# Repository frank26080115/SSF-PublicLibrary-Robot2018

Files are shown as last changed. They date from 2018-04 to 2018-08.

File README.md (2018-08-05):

# SSF-PublicLibrary-Robot2018

This repo contains the hardware, software, and courseware of a small robotics STEM education program. This program is targeting ages 12+, involves 3 live classes held at South San Francisco Public Library, and a robot that's insanely cheap but also incredibly educational.

Perhaps the data here is useful for other educational organizations on a budget.

Please click "Clone or Download" and then "Download ZIP". When the ZIP file is downloaded, unzip it somewhere and open "courseware/index.htm" with a web browser. This will start the course. All the courseware is written as web pages, with pictures, videos, and interactive demos.

The lessons are also hosted on my own website, http://eleccelerator.com/ssfpl_robotics_class_2018/

## Software Required

- Arduino 1.8.1 (this is what SSF Public Library has currently installed)
- Onshape account (free web browser based CAD software that mimics SolidWorks)

## Thanks to: [Microchip Technology](https://www.microchip.com/)

A big thanks to [Microchip Technology](https://www.microchip.com/). These guys manufacture the chip in the middle of your Arduino. My professional contacts at their local office generously donated an insane amount of screwdrivers and backpacks. These classes would not have been possible without their help. Their kindness will not be forgotten.

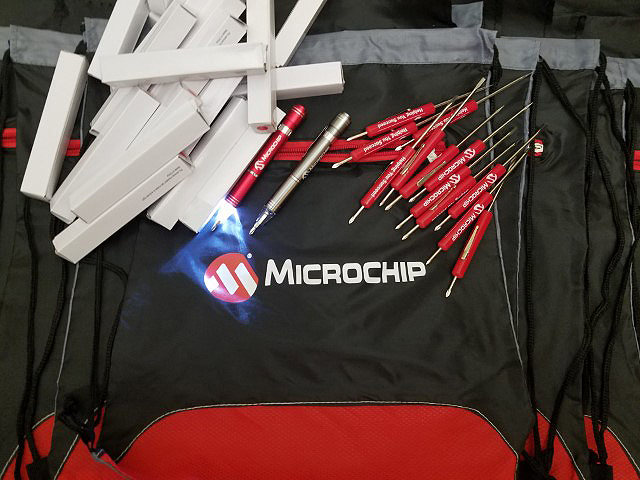
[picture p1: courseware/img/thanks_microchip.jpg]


Personally I thank Microchip for jumpstarting my own path in this hobby and career. Microchip Technology is a huge supporter of STEM programs, I definitely have many of their dev kits simply because they handed them out to me in university. Even when I was a poor highschooler, I got started with their PIC microcontrollers because they were essentially free. I truly believe they are the reason why I am insanely good at writing low-level bare-metal embedded firmware. By the time Arduino Diecimila (the first Arduino with USB) was available, I immediately outgrew the Arduino IDE because of just how far using a PIC has pushed me.

## Thanks to: [Adafruit Industries](https://www.adafruit.com/)

[Adafruit Industries](https://www.adafruit.com/) is a founding pillar of the maker movement from the very beginning, and a [champion for women engineers and entrepreneurs](https://www.adafruit.com/about). Limor "Ladyada" Fried and Phillip Torrone (former senior editor at Make: Magazine, Hackaday, Popular Science, Howtoons) donated all the soldering irons we need that makes these classes possible. These irons are the good stuff, coated tips, adjustable ceramic heaters, fire-proof wiring!

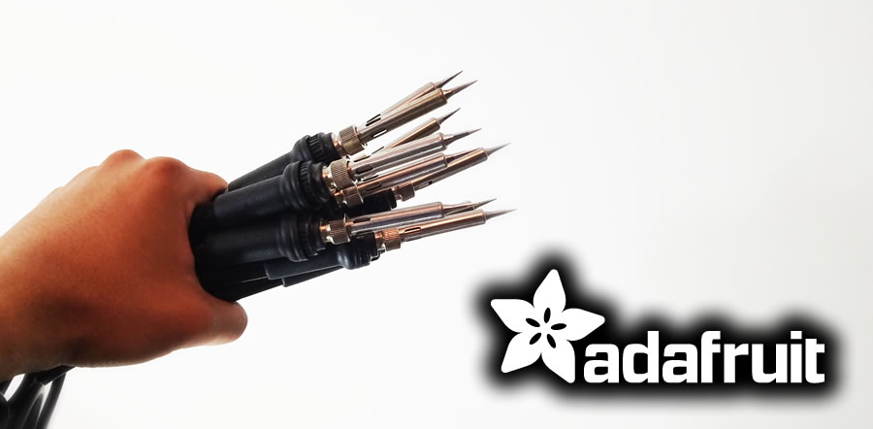
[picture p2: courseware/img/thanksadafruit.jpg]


As a huge supporter of STEAM education, Adafruit Industries have written literally [thousands of guides and tutorials](https://learn.adafruit.com/), along side their amazing collection of products that makes it easy for everyday people to accomplish what used to be impossible. How do I know they are so good? I used to work for Adafruit myself, I wrote some of those tutorials and designed some of those products. Even today my real job's engineering department use their stuff regularly, their breakout boards are just so convenient for quick prototypes. Everything is manufactured proudly on home turf in their New York City office. I recommend all hobbyists to follow [their blog](https://blog.adafruit.com/), it's a good mix of electronics, 3D printing, art, and other fun news.

## Thanks to: [PCBWay](https://www.pcbway.com/)

[PCBWay](https://www.pcbway.com/) is a speedy and cheap PCB manufacturer and electronics assembly company. They generously provided us with multi-colour PCBs for free, so your robots can be pretty and more unique.

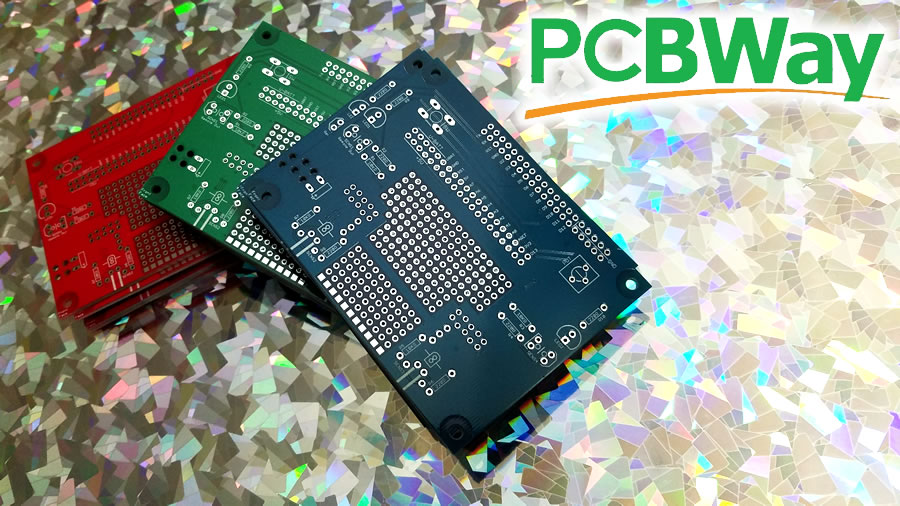
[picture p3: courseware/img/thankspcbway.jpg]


Their service is speedy and at a price that was unheard of before the maker movement took off, making it more accessible to hobbyists and students, allowing the little guys to keep up with the big tech companies. PCBWay also do a lot of [community outreach](https://www.pcbway.com/project/sponsor/) to hobbyists and student teams, hosting contests and offering sponsorships.

Their PCBs are pretty high quality, there's nothing to complain about. Great looking silkscreen. Soldermask and drills are on point. Edges are milled clean. No splatter with the plating. No hassle using their website to order. Each one of our robot PCBs would cost roughly $3.50 each including shipping, and take one week from time-of-order to your doorstep. Great job PCBWay.

## Thanks to: [Silicon Labs](https://www.silabs.com/)

I reached out to people I know at the local [Silicon Labs](https://www.silabs.com/) office, and they gave us a big box of goodies to encourage people to participate in STEM programs at our library.

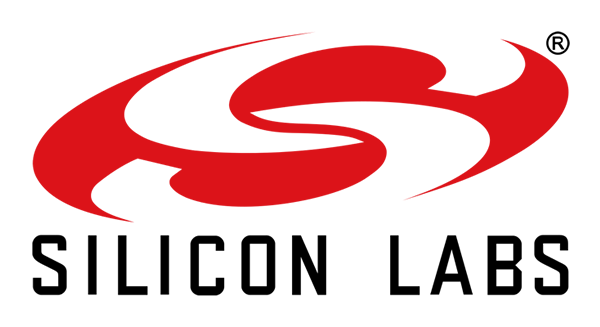
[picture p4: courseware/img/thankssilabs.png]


They are a company who manufacture a lot of different microchips, such as the USB interface chips that hobbyists often use to debug the Raspberry Pi and other embedded Linux platforms. If you are into the drone racing hobby, most likely your drone already has four microcontrollers made by Silicon Labs. They've been growing rapidly in the past decade and is currently well known for having unique, high performance, and low power products, as well as legacy products that are solid and dirt cheap.

## Thanks to: [Hackaday](https://hackaday.com/)

Hackaday always have a special place in my life, providing me with constant motivation and keeping me up-to-date on both my hobby and professional life. They are literally the biggest reason why I am working a dream job in sunny California. I think their blog is inspirational to everybody here and so they gave me a pile of stickers to give to my class!

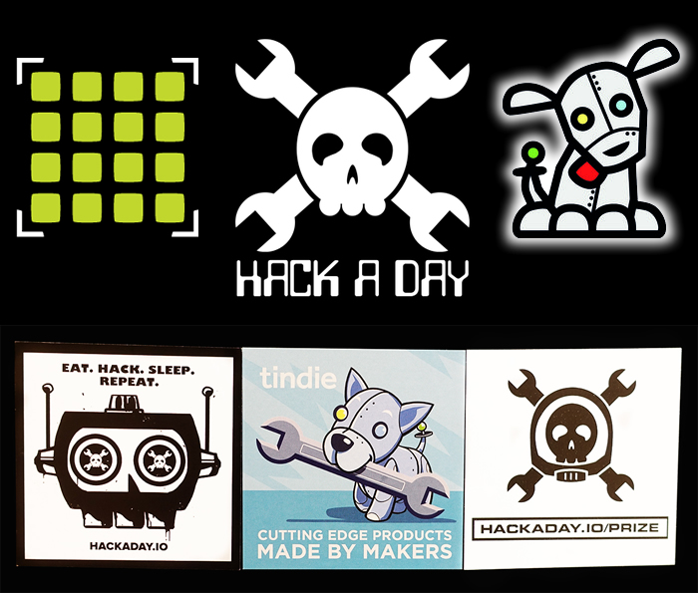
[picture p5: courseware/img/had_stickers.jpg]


They are the host of an excellent online community at [Hackaday.io](https://hackaday.io/), hosts awesome events such as the [Hackaday SuperConference](https://hackaday.com/tag/hackaday-superconference/) and their [Hackaday Prize](https://hackaday.io/prize), and also they run the beloved [Tindie](https://www.tindie.com/) where creative makers and hackers can sell their creations.

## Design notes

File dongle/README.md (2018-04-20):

## What is "dongle"?

The problem is that the library's laptops are locked-down. I can't install device drivers or applications on them, and I can't depend on the library's IT staff to do so either. The Arduino Nanos that cost only $4 each have a CH430 chip as the USB-to-UART converter and that definitely needs a driver to be installed in order to work.

Some form of USB-to-UART is needed in order to communicate with the Arduino Nano bootloader. Ideally, with auto-reset capability.

Well... the library's laptops already have Arduino 1.8.1 installed. Which means that the default virtual COM drivers for Arduino's ATmega8U2 must already be installed as well.

The "dongle" directory contains code for a PSoC that turns it into a USB-to-UART converter. It will use the same VID and PID as the Arduino's ATmega8U2.

The hardware will be the detachable KitProg from Cypress PSoC dev kits. I have plenty of these to give away because we typically break them off from the dev kits at work.

There is no capacitor for the DTS signal that is meant for auto-reset, instead, a simple pulse with a delay simulates the capacitor.

So in the end, for zero cost to me personally, I provide about a dozen USB-to-serial converters to the library that works without additional driver installation. :-)

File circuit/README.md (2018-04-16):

This directory contains the circuit schematic, PCB layout, and PCB gerber files for the robot's circuit board.

The file formats are for CadSoft EAGLE 6.4.0

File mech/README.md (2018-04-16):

This directory includes the STEP, IGES, STL, and GCODE files for the 3D printed body of the robot, and its other parts as well

The actual parametric CAD model of the robot is hosted as public documents on Onshape

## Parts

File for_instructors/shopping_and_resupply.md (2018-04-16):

# Shopping and Resupply

## Tools

### Soldering

There needs to be several soldering irons and accessories for soldering

- soldering iron
- soldering iron stand
- brass wool or damp sponge for cleaning the iron tips
- desoldering braid for fixing mistakes
- desoldering pump for fixing mistakes (not as good as braid but still required)
- solder, rosin core, preferably 60/40 or 63/37 mix
- flush cutters (wire cutters)
- optional: wire strippers capable stripping 26 AWG wire

### Hand Tools

- needle nose plier
- PH0 screwdriver
- hot glue gun

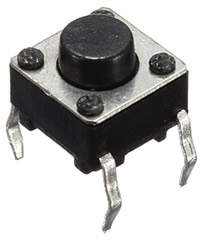
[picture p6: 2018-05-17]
courseware/img/parts/buttonswitch.jpg

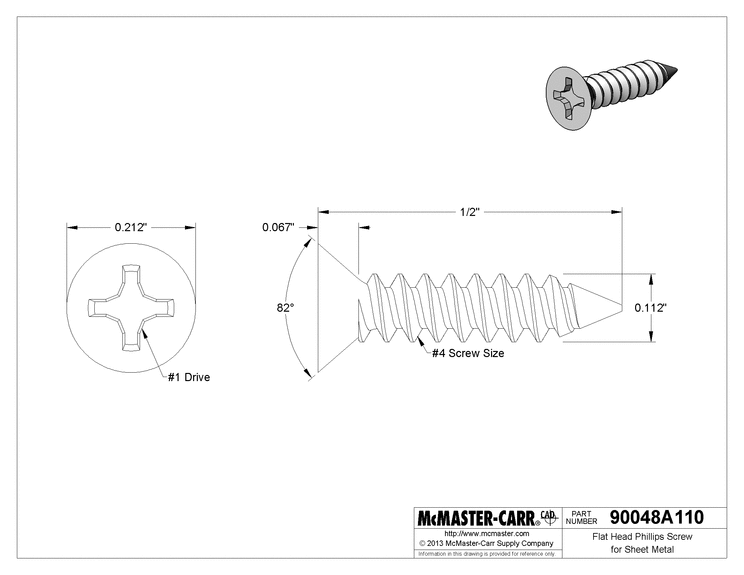
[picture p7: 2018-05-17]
courseware/img/parts/battholderscrew.gif

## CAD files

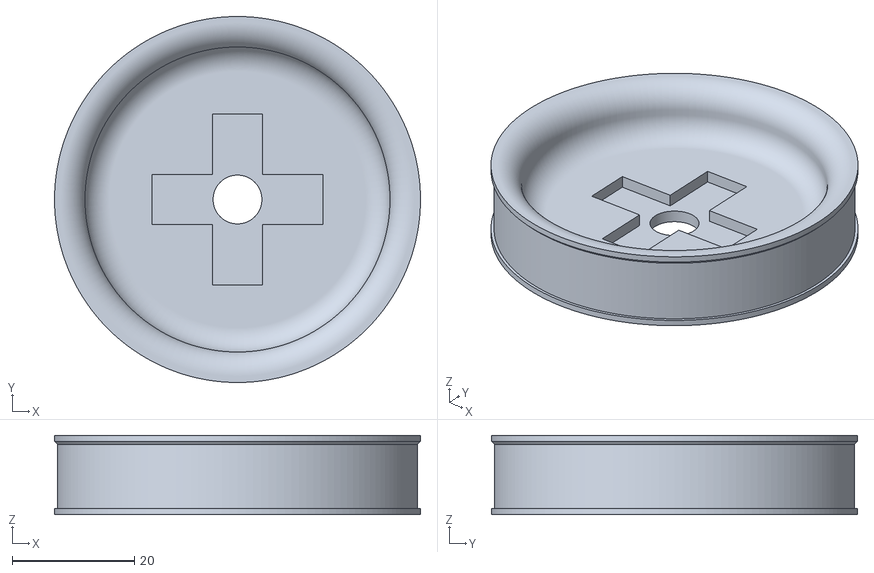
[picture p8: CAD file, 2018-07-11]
mech/wheel_loose.stl
60.0 x 60.0 x 13.0

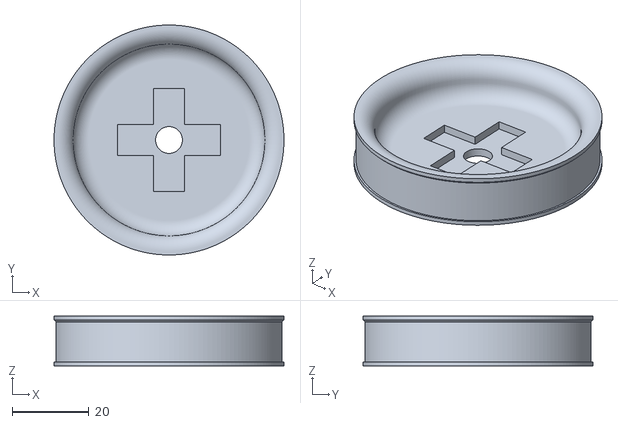
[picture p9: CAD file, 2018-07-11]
mech/wheel.stl
60.0 x 60.0 x 13.0

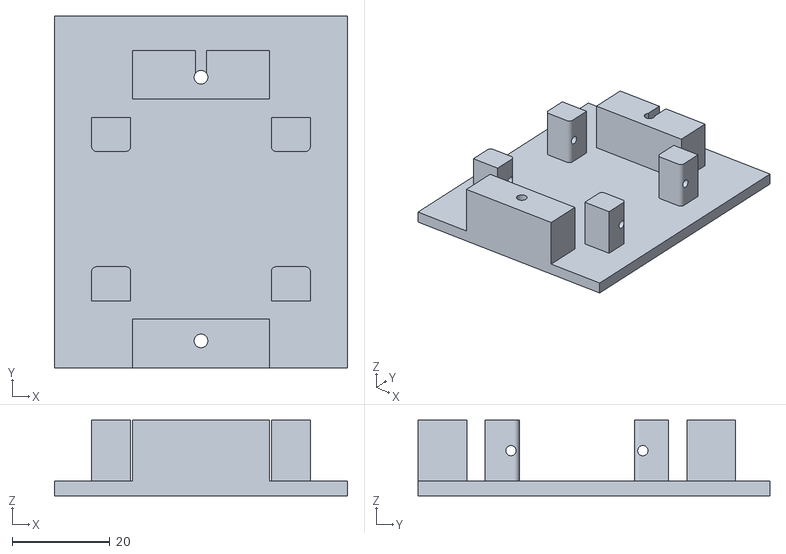
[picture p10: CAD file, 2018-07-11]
mech/robotbody_easierprint.stl
60.0 x 72.0 x 15.5

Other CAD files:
mech/robotbody.stl

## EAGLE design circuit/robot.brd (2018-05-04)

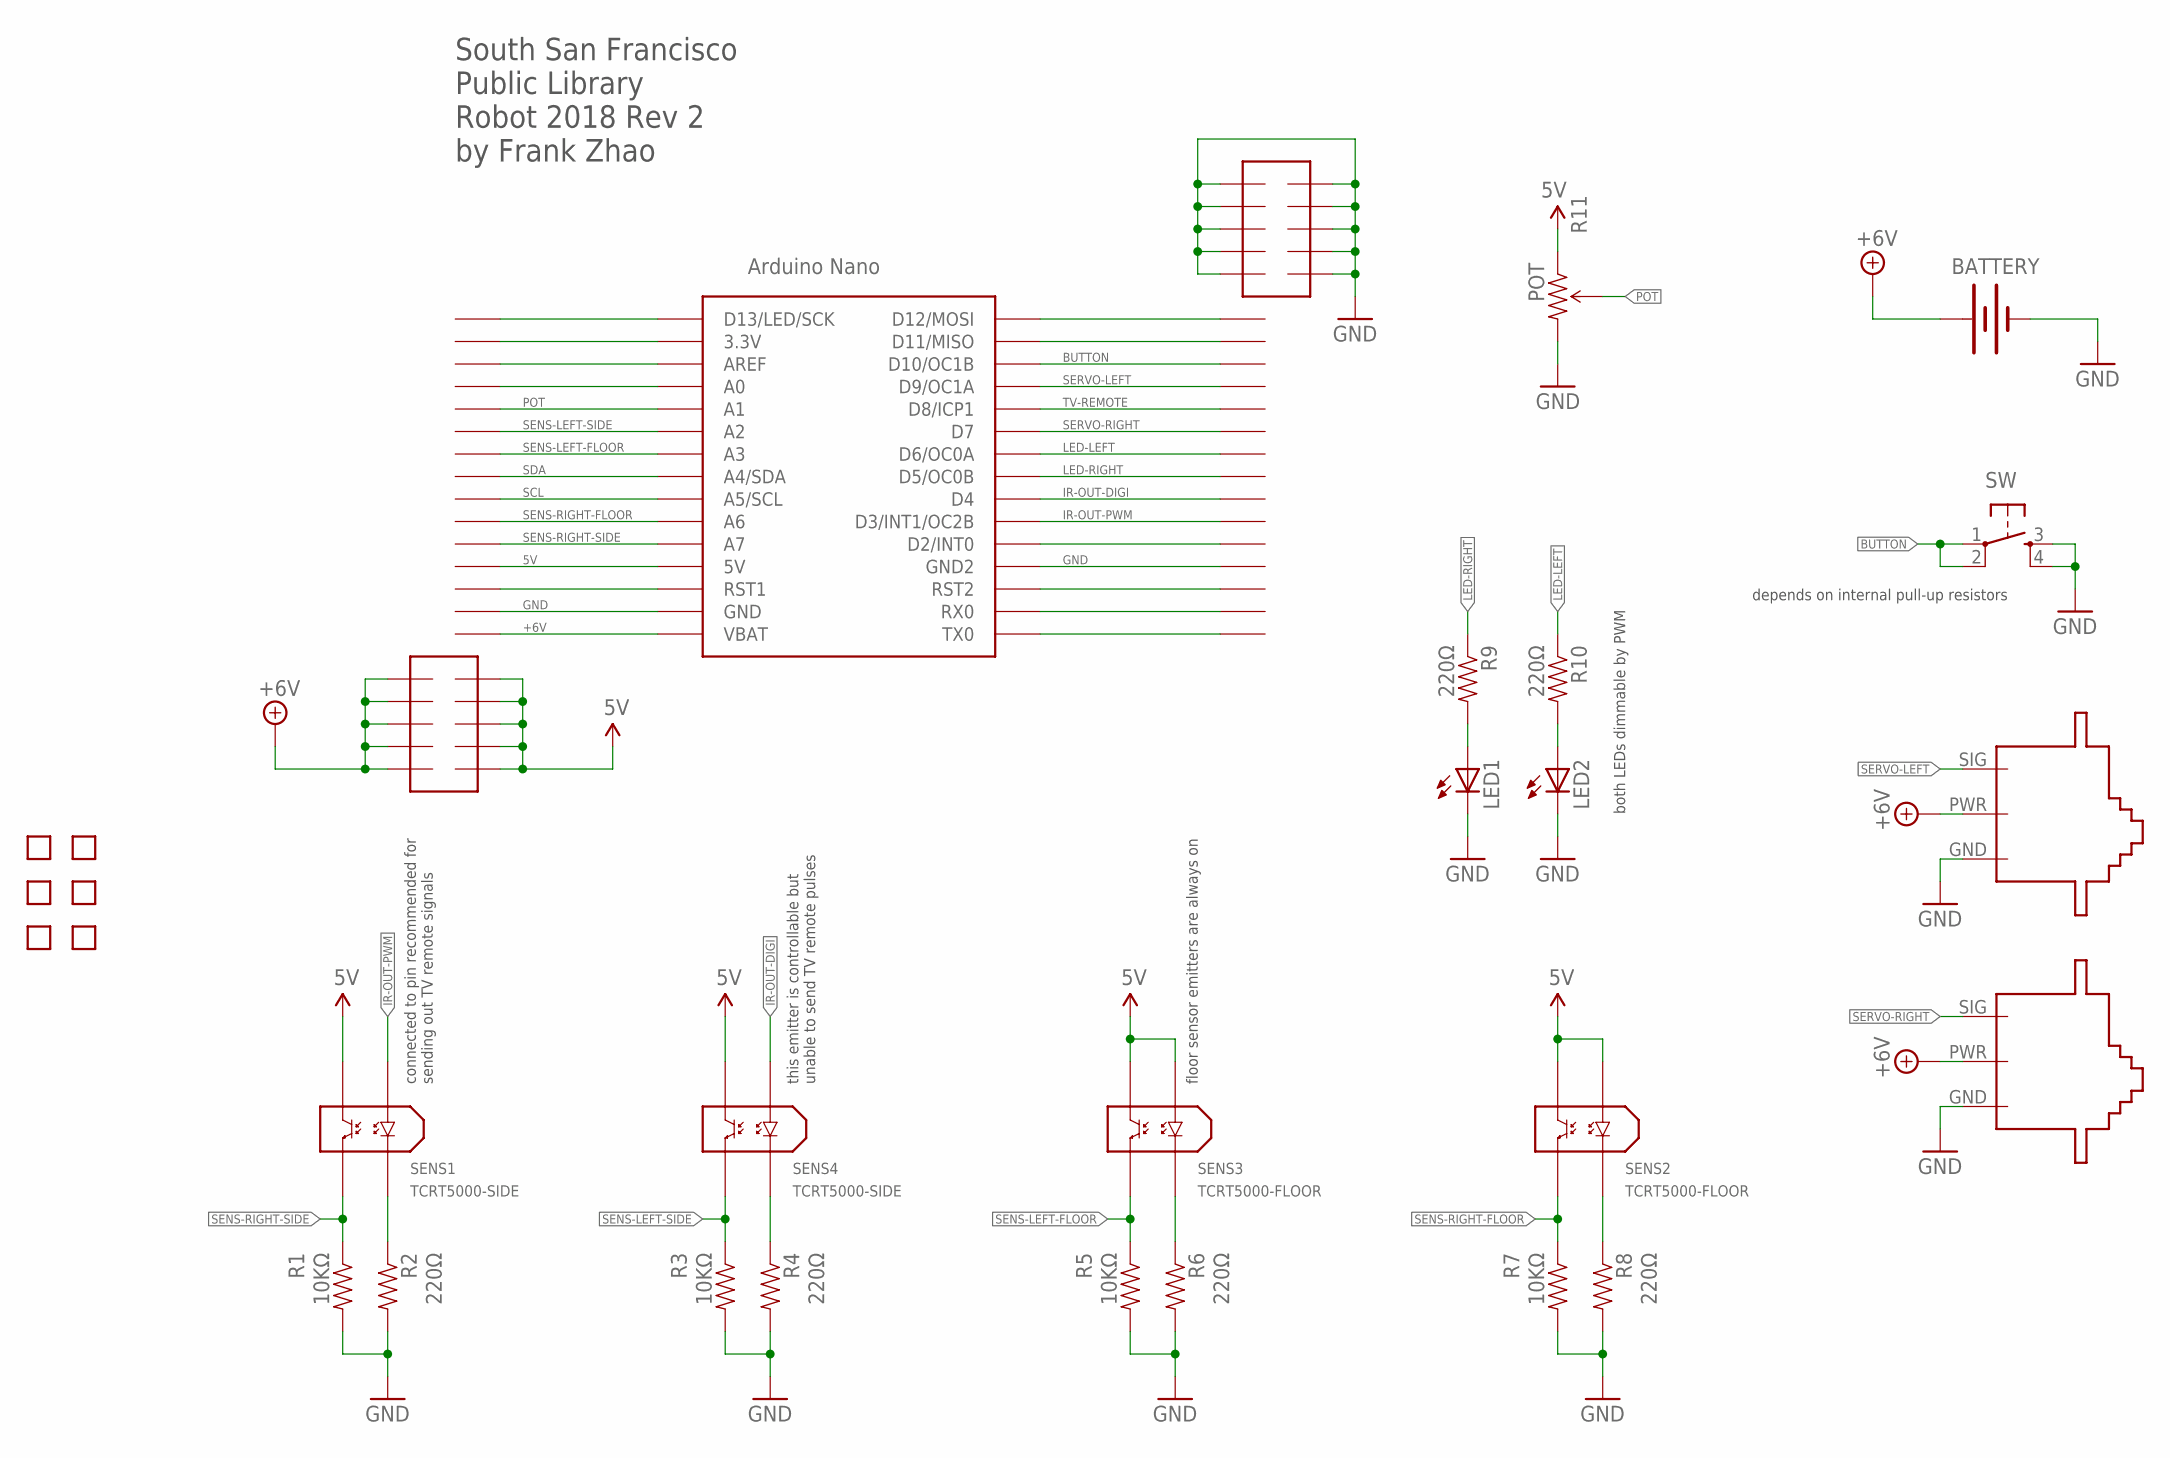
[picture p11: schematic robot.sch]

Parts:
BATTERY: BATTERY-WIRE-CONN; BATT-WIRE-CONN
LED1, LED2: LED5MM
M1: SERVO-FLIPPED
M2: SERVO-1; SERVO
R1, R3, R5, R7: 10KΩ; AXIAL-0.3
R2, R4, R6, R8, R9, R10: 220Ω; AXIAL-0.3
R11: POT; TRIM_POT_PTH
SENS1, SENS4: TCRT5000-SIDE
SENS2, SENS3: TCRT5000-FLOOR
SW: TAC_SWITCHPTH; TACTILE-PTH
U5: NANO
U$1: ROBOT-BODY-HOLDER
U$8: PROTO-AREA-MID; PROTO-AREA-1
U$9: TEXT-INFO
U$10, U$11, U$12, U$13: HOLE; HOLE-2MM
X1, X2: NANO-HEADER-SURROUND

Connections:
5V: R11.1 (CCW), SENS1.COL, SENS2.AN, SENS2.COL, SENS3.AN, SENS3.COL, SENS4.COL, U5.5V, X2.4, X2.E6, X2.E7, X2.E8, X2.E9, X2.E10
+6V: BATTERY.POS (+), M1.PWR, M2.PWR, U5.RAW (VBAT), X2.1, X2.E1, X2.E2, X2.E3, X2.E4, X2.E5
A0: U5.A0, X2.12
BUTTON: SW.1, SW.2, U5.D10 (D10/OC1B), X1.3
GND: BATTERY.NEG (-), LED1.K (C), LED2.K (C), M1.GND, M2.GND, R1.P$2 (2), R2.P$2 (2), R3.P$2 (2), R4.P$2 (2), R5.P$2 (2), R6.P$2 (2), R7.P$2 (2), R8.P$2 (2), R11.3 (CW), SW.3, SW.4, U5.GND, U5.GND1 (GND2), X1.12, X1.E1, X1.E2, X1.E3, X1.E4, X1.E5, X1.E6, X1.E7, X1.E8, X1.E9, X1.E10, X2.2
IR-OUT-DIGI: SENS4.AN, U5.D4, X1.9
IR-OUT-PWM: SENS1.AN, U5.D3 (D3/INT1/OC2B), X1.10
LED-LEFT: R10.P$1 (1), U5.D6 (D6/OC0A), X1.7
LED-RIGHT: R9.P$1 (1), U5.D5 (D5/OC0B), X1.8
unnamed: R2.P$1 (1), SENS1.CAT
unnamed: R4.P$1 (1), SENS4.CAT
unnamed: R6.P$1 (1), SENS3.CAT
unnamed: R8.P$1 (1), SENS2.CAT
unnamed: LED1.A, R9.P$2 (2)
unnamed: LED2.A, R10.P$2 (2)
unnamed: U5.3.3V, X2.14
unnamed: U5.AREF, X2.13
unnamed: U5.RST (RST1), X2.3
unnamed: U5.D13 (D13/LED/SCK), X2.15
unnamed: U5.D12 (D12/MOSI), X1.1
unnamed: U5.D11 (D11/MISO), X1.2
unnamed: U5.D2 (D2/INT0), X1.11
unnamed: U5.RST1 (RST2), X1.13
unnamed: U5.RX0, X1.14
unnamed: U5.TX0, X1.15
POT: R11.2 (WIPER), U5.A1, X2.11
SCL: U5.A5 (A5/SCL), X2.7
SDA: U5.A4 (A4/SDA), X2.8
SENS-LEFT-FLOOR: R5.P$1 (1), SENS3.EM, U5.A3, X2.9
SENS-LEFT-SIDE: R3.P$1 (1), SENS4.EM, U5.A2, X2.10
SENS-RIGHT-FLOOR: R7.P$1 (1), SENS2.EM, U5.A6, X2.6
SENS-RIGHT-SIDE: R1.P$1 (1), SENS1.EM, U5.A7, X2.5
SERVO-LEFT: M2.SIG, U5.D9 (D9/OC1A), X1.4
SERVO-RIGHT: M1.SIG, U5.D7, X1.6
TV-REMOTE: U5.D8 (D8/ICP1), X1.5

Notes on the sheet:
connected to pin recommended for sending out TV remote signals
this emitter is controllable but unable to send TV remote pulses
floor sensor emitters are always on
depends on internal pull-up resistors
both LEDs dimmable by PWM

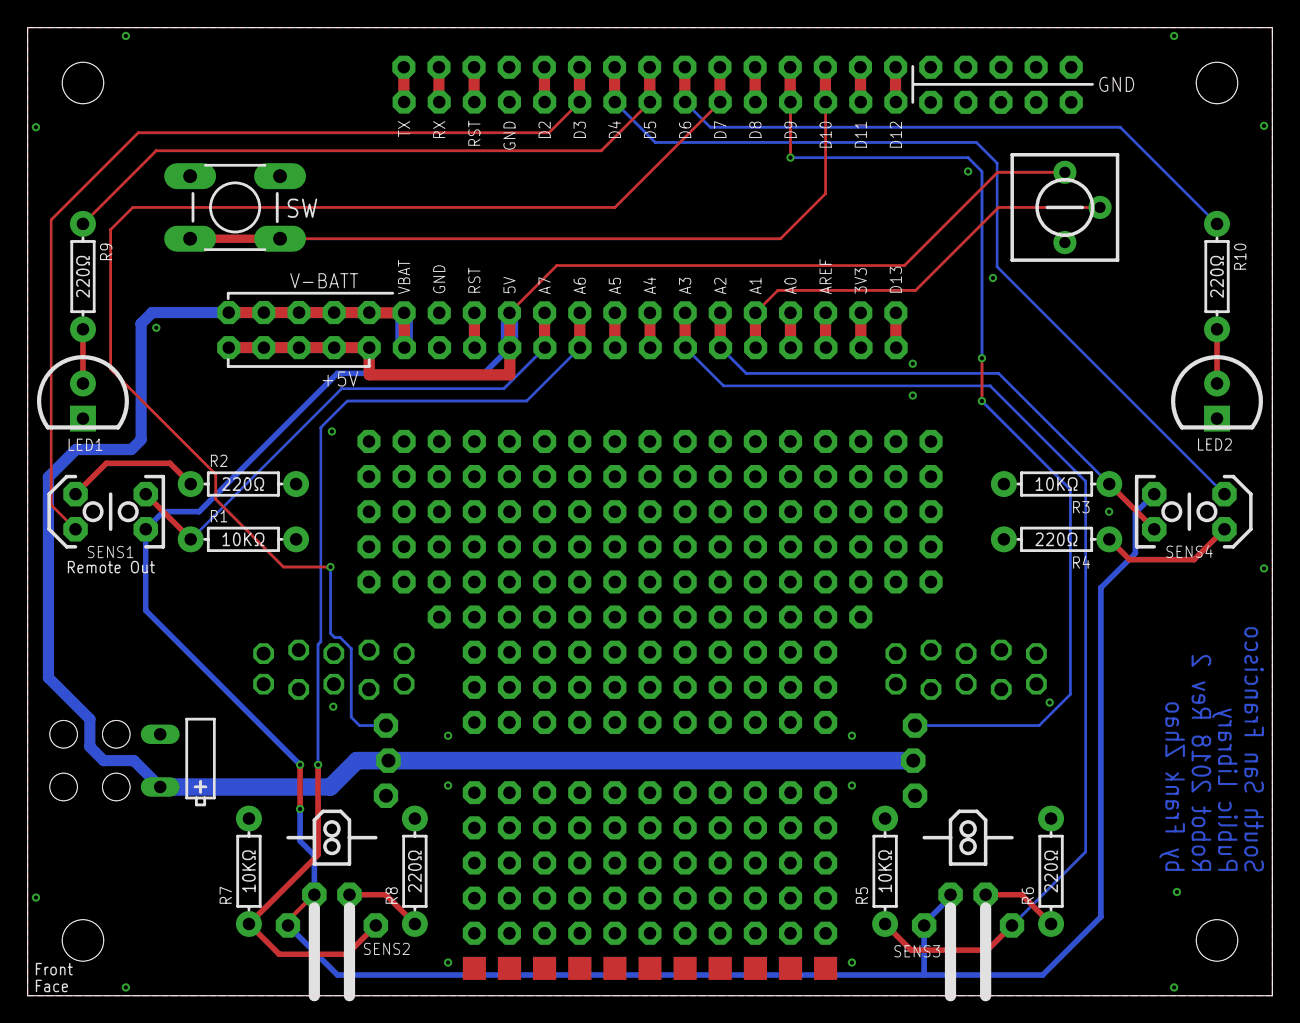
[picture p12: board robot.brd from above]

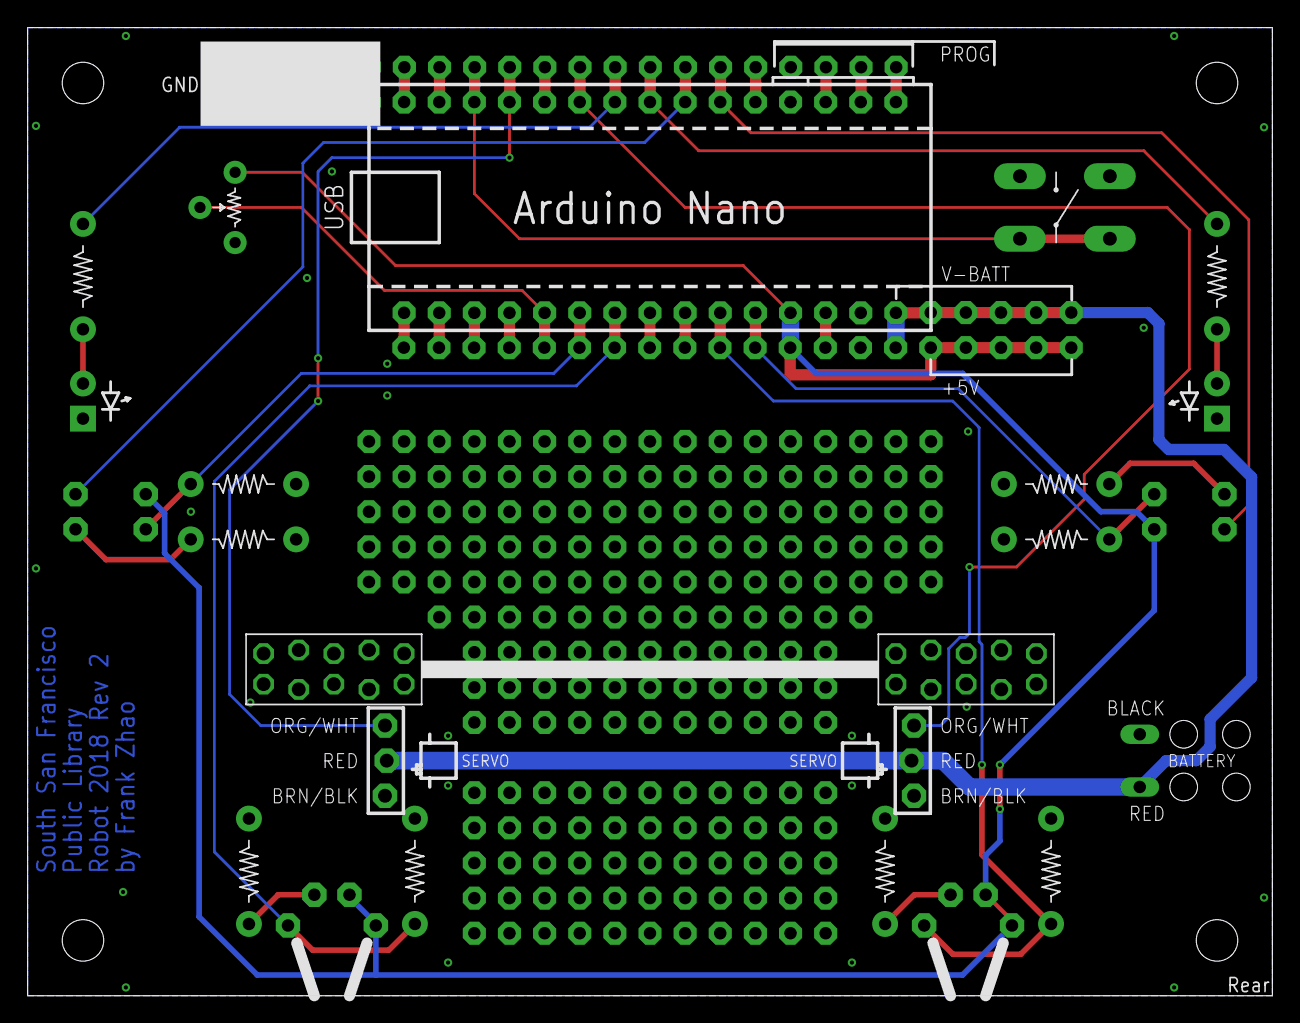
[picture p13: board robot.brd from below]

Board: 2 copper layers, 90.0 x 70.0 mm, 31 parts (7 on the bottom side), 35 nets.

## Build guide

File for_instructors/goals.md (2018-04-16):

# Goals

### Works at SSF Public Library

Everything is designed taking into account what the library can and cannot do. The class size limit accounts for the room size and staff availability. The complexity of a class is designed around 1 hour sessions. The software used is either web browser based or already installed on the library computers. 

### Extended Learning

The robot can be expanded upon. Components can be added to the circuit board, and a breadboard can be stuck to the back of the robot. Extra lessons can be given to students who wants to do upgrades.

Participants will compete in line-following races and mini sumo wrestling. They are encouraged to come back with improvements and a leader board will be kept for the small community. 

### Economical

All the components of the robot are dirt cheap, available in bulk from AliExpress, Amazon, or eBay. Leftover components can be used later for a repeat of the program or for other programs. Many of the components are already in the SSF Public Library's inventory.

We want hobby robotics to appear cheap and accessible to everyone. Which also encourages continued learning.

The time per class is carefully minimized while maximizing concepts being taught. The rooms at the library are shared between many different programs, the only class that requires a room is the soldering session. The rest can take place in a quiet corner of the library.

### Instant Gratification

Success encourages more success. At every step, the student should feel like they have accomplished something. The live soldering class will attempt to get the robot moving as soon as possible.

This library does have two 3D printers that can be used to print what the students create.

### Ease of Instruction

Videos are prepared well ahead of the class, while live demonstration is still used. The videos are short loops that can be left on a projector. This will allow the instructor (me) to help a pupil while other pupils can still watch the videos, or even skip ahead while the instructor helps somebody who is slightly behind.

The videos are silent with text captions. Good for accessibility, and a library.

The circuit board is well labeled with graphics that minimizes chances of mistakes.

NO MATH ALLOWED IN MY COURSEWARE :-) we don't want to bore anybody

### Starting from Minimal Components

The robot kits on Amazon all feel like good deals, but they don't teach anything. Those are all designed to look like you are getting "value" with a lot of parts, and made hard to fail at so they get good 5 star reviews. In doing so, they hide a lot of concepts that enable creativity.

For example, most of those kits on Amazon feature a TCRT5000 sensor but they are pre-assembled into a comparator circuit that outputs 1 or 0. Whereas the class here will link the concept of a potentiometer voltage divider to the phototransistor replacing one of two resistors in a voltage divider, thus forming an amplifier that reacts to light.

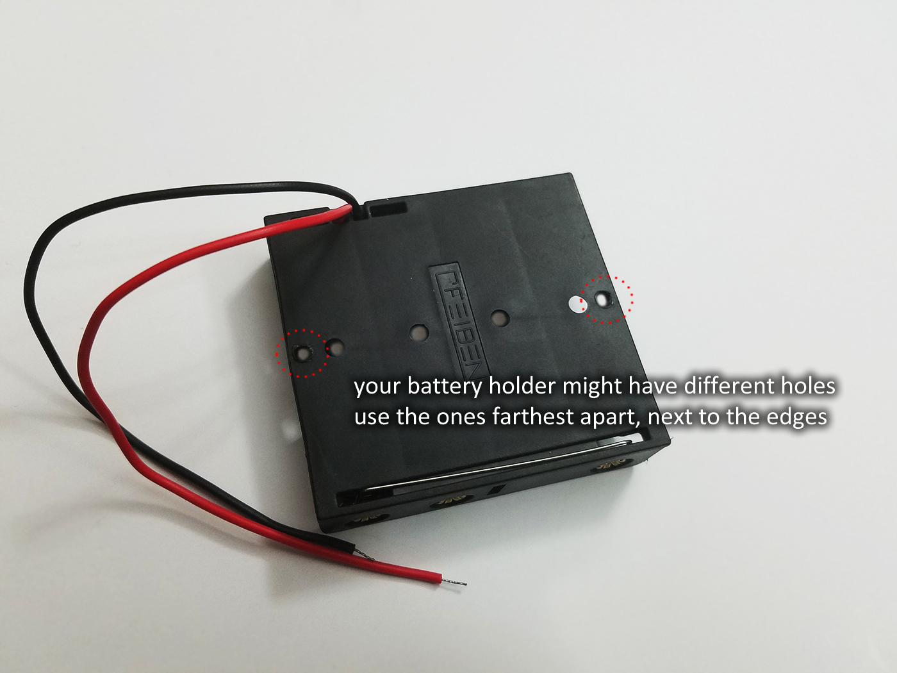
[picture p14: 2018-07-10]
courseware/img/instruct/battholder_diffholes.jpg

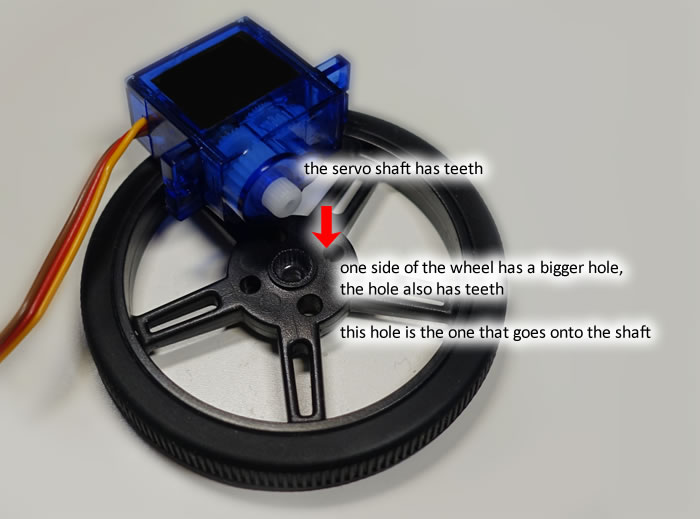
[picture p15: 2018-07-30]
courseware/img/instruct/servoshaftteeth.jpg

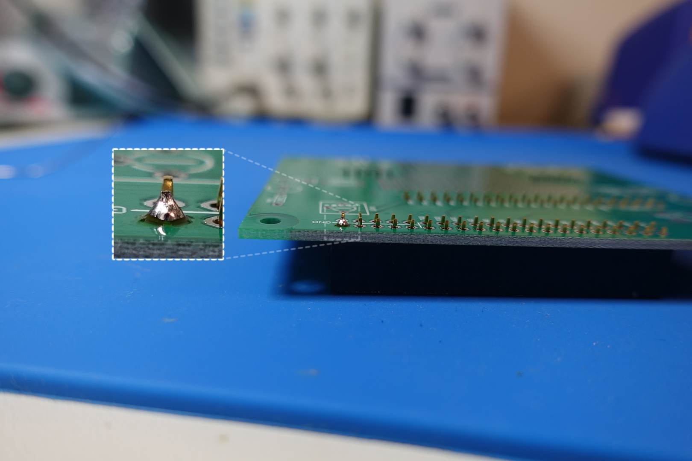
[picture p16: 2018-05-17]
courseware/img/instruct/one_zoomed_in_solder_joint.png

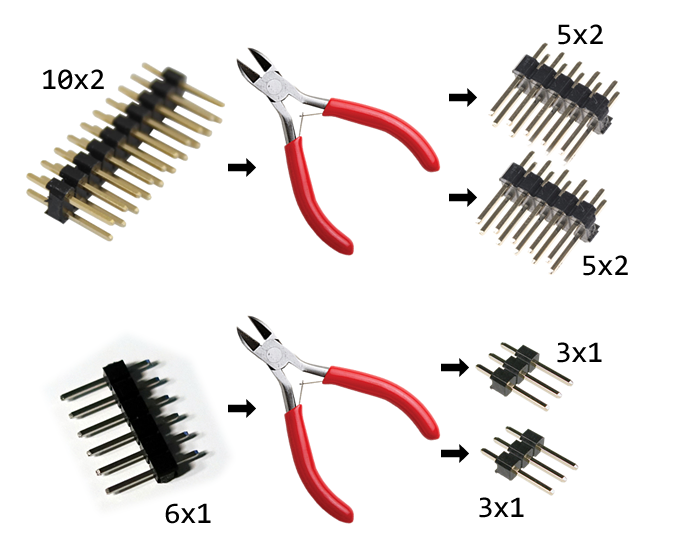
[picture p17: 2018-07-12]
courseware/img/instruct/cutting_headers.fw.png

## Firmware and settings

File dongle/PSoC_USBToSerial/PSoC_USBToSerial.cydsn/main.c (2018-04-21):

/*******************************************************************************
* File Name: main.c
*
* Version: 2.0
*
* Description:
*   The component is enumerated as a Virtual Com port.
*   Acts as a USB-to-UART converter for use with Arduino
*
* Related Document:
*  Universal Serial Bus Specification Revision 2.0
*  Universal Serial Bus Class Definitions for Communications Devices
*  Revision 1.2
*
********************************************************************************
* Copyright 2015, Cypress Semiconductor Corporation. All rights reserved.
* This software is owned by Cypress Semiconductor Corporation and is protected
* by and subject to worldwide patent and copyright laws and treaties.
* Therefore, you may use this software only as provided in the license agreement
* accompanying the software package from which you obtained this software.
* CYPRESS AND ITS SUPPLIERS MAKE NO WARRANTY OF ANY KIND, EXPRESS OR IMPLIED,
* WITH REGARD TO THIS SOFTWARE, INCLUDING, BUT NOT LIMITED TO, NONINFRINGEMENT,
* IMPLIED WARRANTIES OF MERCHANTABILITY AND FITNESS FOR A PARTICULAR PURPOSE.
*******************************************************************************/

#include <project.h>
#include "stdio.h"

#define USBFS_DEVICE    (0u)

/* The buffer size is equal to the maximum packet size of the IN and OUT bulk
* endpoints.
*/
#define USBUART_BUFFER_SIZE (64u)

volatile uint32 millis = 0;
volatile uint32 secs = 0;

#define CLKDIV_BAUD_115200    69
#define CLKDIV_BAUD_230400    35
#define CLKDIV_BAUD_250000    32
#define CLKDIV_BAUD_500000    16
#define CLKDIV_BAUD_1000000    8
#define CLKDIV_BAUD_1500000    5
#define CLKDIV_BAUD_57600    139
#define CLKDIV_BAUD_38400    208
#define CLKDIV_BAUD_28800    278
#define CLKDIV_BAUD_19200    417
#define CLKDIV_BAUD_14400    556
#define CLKDIV_BAUD_9600     833
#define CLKDIV_BAUD_4800    1667
#define CLKDIV_BAUD_2400    3333
#define CLKDIV_BAUD_1200    6667
#define CLKDIV_BAUD_800    10000
#define CLKDIV_BAUD_600    13333
#define CLKDIV_BAUD_300    26667
#define CLKDIV_BAUD_150    53333

uint32_t Baud_to_Divider(uint32_t baud);

/*******************************************************************************
* Function Name: main
********************************************************************************
*
* Summary:
*  The main function performs the following actions:
*   1. Waits until VBUS becomes valid and starts the USBFS component which is
*      enumerated as virtual Com port.
*   2. Waits until the device is enumerated by the host.
*   3. Waits for data coming from the hyper terminal and sends it back.
*   4. PSoC3/PSoC5LP: the LCD shows the line settings.
*
* Parameters:
*  None.
*
* Return:
*  None.
*
*******************************************************************************/
int main()
{
    uint16 count;
    uint8 buffer[USBUART_BUFFER_SIZE];

    uint8 prevLines = 0; // tracks previous DTS status
    
    CyGlobalIntEnable;

    ExternReset_SetDriveMode(ExternReset_DM_OD_HI);
    ExternReset_Write(1);
    
    UART_Start();

    /* Start USBFS operation with 5-V operation. */
    USBUART_Start(USBFS_DEVICE, USBUART_5V_OPERATION);
    USBUART_EnableSofInt();

    for(;;)
    {
        /* Host can send double SET_INTERFACE request. */
        if (0u != USBUART_IsConfigurationChanged())
        {
            /* Initialize IN endpoints when device is configured. */
            if (0u != USBUART_GetConfiguration())
            {
                /* Enumeration is done, enable OUT endpoint to receive data 
                 * from host. */
                USBUART_CDC_Init();
            }
        }

        /* Service USB CDC when device is configured. */
        if (0u != USBUART_GetConfiguration())
        {
            static uint32_t prevBaud = 0;
            uint32_t curBaud = USBUART_GetDTERate();
            // check if baud rate has changed
            if (prevBaud != curBaud)
            {
                uint32_t clkDivider = Baud_to_Divider(curBaud);
                if (clkDivider <= 0) {
                    clkDivider = 1;
                }
                else if (clkDivider > 0x10000) {
                    clkDivider = 0x10000;
                }
                UART_CLOCK_SetDividerValue(clkDivider);
                prevBaud = curBaud;
            }

            // check if parity bits settings have changed
            static uint32_t prevParity = USBUART_PARITY_NONE;
            uint32_t curParity = USBUART_GetParityType();
            if (prevParity != curParity)
            {
                uint32_t newParity = UART__B_UART__NONE_REVB;
                prevParity = curParity;
                if (curParity == USBUART_PARITY_NONE)
                {
                    newParity = UART__B_UART__NONE_REVB;
                }
                else if (curParity == USBUART_PARITY_EVEN)
                {
                    newParity = UART__B_UART__EVEN_REVB;
                }
                else if (curParity == USBUART_PARITY_ODD)
                {
                    newParity = UART__B_UART__ODD_REVB;
                }
                else if (curParity == USBUART_PARITY_MARK)
                {
                    newParity = UART__B_UART__MARK_SPACE_REVB;
                }
                else if (curParity == USBUART_PARITY_SPACE)
                {
                    newParity = UART__B_UART__MARK_SPACE_REVB;
                }

                UART_WriteControlRegister((UART_ReadControlRegister() & (uint8)~UART_CTRL_PARITY_TYPE_MASK)
                        | (uint8)(newParity << UART_CTRL_PARITY_TYPE0_SHIFT));
            }

            /* Check for input data from host. */
            if (0u != USBUART_DataIsReady())
            {
                /* Read received data and re-enable OUT endpoint. */
                count = USBUART_GetAll(buffer);

                if (0u != count)
                {
                    // check for changes in DTS control line signal
                    uint16 curLines = USBUART_GetLineControl();
                    if ((prevLines & USBUART_LINE_CONTROL_DTR) == 0 && (curLines & USBUART_LINE_CONTROL_DTR) != 0)
                    {
                        ExternReset_SetDriveMode(ExternReset_DM_OD_LO);
                        ExternReset_Write(0);
                        // delay for reset pulse to register
                        for (int i = 0; i < 1; i++)
                        {
                            CyDelayUs(100);
                        }
                        ExternReset_Write(1);
                        ExternReset_SetDriveMode(ExternReset_DM_OD_HI);

                        // delay for bootloader to get ready
                        for (int i = 0; i < 1; i++)
                        {
                            CyDelayUs(1000);
                        }
                    }
                    prevLines = curLines; // for comparison on next loop

                    UART_PutArray(buffer, count);
                }
            }

            if (UART_GetRxBufferSize() > 0) // something to read
            {
                unsigned int idx = 0;
                // read all possible
                for (idx = 0; idx < USBUART_BUFFER_SIZE && UART_GetRxBufferSize() > 0; idx++)
                {
                    buffer[idx] = UART_ReadRxData();
                }

                /* Wait until component is ready to send data to host. */
                while (0u == USBUART_CDCIsReady())
                {
                }

                /* Send data back to host. */
                USBUART_PutData(buffer, idx);
            }
        }
    }
}

void USBUART_SOF_ISR_ExitCallback(void)
{
    millis++;
    if (millis >= 1000)
    {
        secs++;
        millis = 0;
    }
}

uint32_t Baud_to_Divider(uint32_t baud)
{
    uint32_t masterClk = BCLK__BUS_CLK__HZ;
    uint32_t baudDiv2;
    uint32_t result;
    if (baud <= 0)
    {
        baud = 1;
    }
    baud *= 8;
    baudDiv2 = baud / 2;
    result = masterClk + baudDiv2;
    result /= baud;
    return result;
}

/* [] END OF FILE */

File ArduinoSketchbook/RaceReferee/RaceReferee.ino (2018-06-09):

#include <BookWorm.h>
#include <LiquidCrystal_I2C.h>
#include <Wire.h>

LiquidCrystal_I2C lcd(0x3F, 16, 2); // 16 column by 2 line LCD, with I2C address of 0x3F

#define pinLightSensor 0

// defining the states available in our state machine
// see switch-statement inside loop() later
enum
{
  STATEMACH_START_WAITING = 0,
  STATEMACH_START_PRIMED,
  STATEMACH_STARTED_UNSURE,
  STATEMACH_RUNNING,
  STATEMACH_ENDED,
};

void setup()
{
  BookWorm.begin();
  Wire.begin();

  PORTC &= ~(_BV(4) | _BV(5)); // prevent internal pull-up resistors from damaging anything

  lcd.init();
  PORTC &= ~(_BV(4) | _BV(5)); // prevent internal pull-up resistors from damaging anything, again, just in case

  lcd.backlight();

  lcd_bigNumInit(); // the big number clock trick requires loading custom characters into the LCD memory
  startMessage();
}

void loop()
{
  static int state = STATEMACH_START_WAITING;
  static uint32_t lastLcdTime = 0;
  static uint32_t startTime = 0;
  static uint32_t endTime = 0;
  uint32_t curMillis, dispMillis;
  bool seeLight;
  if (BookWorm.isButtonPressed())
  {
    state = STATEMACH_START_WAITING;
    startMessage();
    do
    {
      delay(200);
    }
    while (BookWorm.isButtonPressed());
  }

  curMillis = millis();
  seeLight = readLightSensor();

  /*
   * it's hard to explain state machines with just code comments
   * please read https://www.sparkfun.com/news/1801
   * which is an article about state machines, along with a simple example
   * 
   * also here's the article on switch-case statements
   * https://www.arduino.cc/reference/en/language/structure/control-structure/switchcase/
   */
  switch (state)
  {
    case STATEMACH_START_WAITING:
      if (readLightSensor() == false)
      {
        state = STATEMACH_START_PRIMED;
        lcd.setCursor(0, 1);
        lcd.print(F("Go! Go! Go! Go! "));
        lcd.setCursor(0, 0);
        lcd.print(F("                "));
      }
      break;
    case STATEMACH_START_PRIMED:
      
      if (seeLight != false)
      {
        state = STATEMACH_STARTED_UNSURE;
        startTime = curMillis;
      }
      break;
    case STATEMACH_STARTED_UNSURE:
      if (seeLight == false)
      {
        startTime = curMillis;
      }
      dispMillis = curMillis - startTime;
      if (dispMillis > 2000)
      {
        state = STATEMACH_RUNNING;
      }
      break;
    case STATEMACH_RUNNING:
      dispMillis = curMillis - startTime;
      if (seeLight == false)
      {
        endTime = curMillis;
        state = STATEMACH_ENDED;
      }
      break;
    case STATEMACH_ENDED:
      dispMillis = endTime - startTime;
      break;
  }

  curMillis = millis();
  if (state == STATEMACH_STARTED_UNSURE || state == STATEMACH_RUNNING || state == STATEMACH_ENDED)
  {
    if ((curMillis - lastLcdTime) >= 100) // only update the LCD when we need to
    {
      bool dots = state == STATEMACH_STARTED_UNSURE || state == STATEMACH_RUNNING;
      if (state == STATEMACH_ENDED)
      {
        // blink the dots if the race has finished
        // the code below is a bit of math that changes between true and false every half second
        dots = ((curMillis / 500) % 2) == 0;
      }

      lastLcdTime = curMillis;
      lcd_printTime(dispMillis, 1, dots);
    }
  }
}

bool readLightSensor()
{
  // the concept of hysteresis is best explained as a threshold that changes, so actually two thresholds, which one being used depends on the previous output state
  // this is used here to prevent any noise we get from the light sensor from confusing our readings when the light brightness transitions slowly
  #define LASER_HYSTERESIS 16
  static bool latched = false;
  
  int x = analogRead(pinLightSensor);
  int thresh = BookWorm.readPotentiometer();
  BookWorm.printf(F("light: %d ; pot: %d\r\n"), x, thresh); // show on computer screen

  // change latched output according to brightness, using hysteresis
  if (latched == false)
  {
    if (x < (thresh - (LASER_HYSTERESIS / 2)))
    {
      latched = true;
    }
  }
  else // latched == true
  {
    if (x > (thresh + (LASER_HYSTERESIS / 2)))
    {
      latched = false;
    }
  }

  // use LEDs to indicate status of sensor, without using hysteresis
  if (x > thresh)
  {
    BookWorm.setLedLeftOff();
    BookWorm.setLedRightOff();
  }
  else // latched == true
  {
    BookWorm.setLedLeftOn();
    BookWorm.setLedRightOn();
  }

  return latched;
}

void startMessage()
{
  lcd.setCursor(0, 0);
  lcd.print(F("Waiting to Start!"));
  lcd.setCursor(0, 1);
  lcd.print(F("                "));
}

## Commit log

2018-04-16 initial commit
    some readmes, some arduino libs, all elec
    [robot-10-bottom_copper.GBL, robot-3-top_solderpaste.GTP, robot-4-top_soldermask.GTS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]
2018-04-18 continousservo accel works, added IR codes
    continuous servo works
2018-04-18 new bootloader with button hold
2018-04-19 add ext reset to avr usb2ser
    [main.c]
2018-04-21 real Arduino VID PID used
    previous one pulled from repo was not real
2018-04-21 added parity bits change to dongle
    fixed prevbaud not changing
    removed PSoC3 and PSoC4
    [main.c]
2018-05-03 dongle RX pin changed to pull-up resistor
2018-05-04 circuit error: flipped floor sensor footprint
    [robot.brd, robot.sch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]
2018-05-05 adding PID arduino library
2018-05-05 changes to servo code, added IMU code, other small changes
    added back LED
    not tested but compiles without error
2018-05-14 start of circuit basics class
2018-05-16 single sensor test rig
2018-05-16 almost finalized 3D CAD class
2018-05-16 circuit lesson contents
2018-05-17 elec class and assembly class
2018-05-17 adjusted soldering diagram
2018-05-20 more class content
    desoldering 2, tires, breadboard
2018-05-21 incomplete class content for Arduino
2018-05-21 new soldering graphics
2018-05-24 small bit more class content
    colour spectrum, excercise 2 flow chart
2018-05-25 more class content
    dongle images, smaller screenshots, gif of LED blinking
2018-05-25 adjustment to soldering comic instructions
2018-05-26 almost done arduino class
2018-05-27 gfx for arduino nano pinout
2018-05-27 muted videos inside arduino class
2018-05-28 more course content, IR remote, PCBs, and others
2018-05-29 flip one servo for corrected drive direction
2018-05-29 changes to PCB information
2018-05-29 added finished robot and PCB images
2018-05-29 fixed links in Arduino class
2018-05-30 added missing blinking test, added github links
    [HardwareTestLEDsBlink.ino]
2018-05-31 ir out pin gfx, more websites to learn from, fixed a typo
2018-05-31 start circuit lesson with a finished picture
2018-06-05 more circuit gifs
2018-06-13 edited sponsor, added PCBWay, better photos
2018-06-13 minor change to PCBWay blurb
2018-06-19 bluetooth demo turned too slow
    [DrivingCommands.ino]
2018-06-19 restored IR remote pin default pull resistor
2018-06-22 tiny pcbway blurb edit
2018-06-22 printable URL, other robot competitions, minor front page changes
2018-06-30 got rid of unfinished arduino code files
2018-07-04 missed a renamed function call
    [SingleSensorTestRig.ino]
2018-07-06 3d printed wheel
2018-07-06 added temporary no pulse for servo stop
2018-07-06 another line for solder safety
2018-07-06 fixed cont. servo calib. tool bug with no-pulse default
    [ContinuousServoCalibrationTool.ino]
2018-07-09 corrected order of hole creation in CAD class
2018-07-09 alternative pin slot video, shortened prev vid too
2018-07-09 added 3D CAD mouse tutorial
2018-07-10 note for when the battery holder has different holes
2018-07-10 made circuit advanced class more prominent
2018-07-11 mech changes, added wheels, added more gcode
    [robotbody_easierprint.stl, wheel.stl, wheel_loose.stl]
2018-07-12 better images involving headers soldering
2018-07-12 images to show finished solder joints
2018-07-12 image for resistor values
2018-07-14 more info in rechargable battery page
2018-07-16 10kohm resistor image was wrong
2018-07-16 new pic for front page, and added rechargable battery class link
2018-07-16 more verbose instruction on header soldering
2018-07-17 fixed bug with no pulse on stop for servos
2018-07-22 added image for resistor soldering instructions
2018-07-30 new images regarding servo installation
2018-08-03 instructions for mac arduino drivers
2018-08-05 added another mistake prevention image to CAD class
2018-08-14 added another circuit homework question
